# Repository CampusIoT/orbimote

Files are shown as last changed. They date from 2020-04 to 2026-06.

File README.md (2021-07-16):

# OrbiMote: open-sourced LoRaWAN high-altitude balloon (HAB) tracker

"urbi et orbi" : to the city and the world

The Orbimote is a LoRa/LoRaWAN endpoint
* for tracking sounding balloons
* and for implementing flying repeaters and flying field testers.

# HW & FW
* [Hardware](./hardware)
* [Firmware](./firmware)

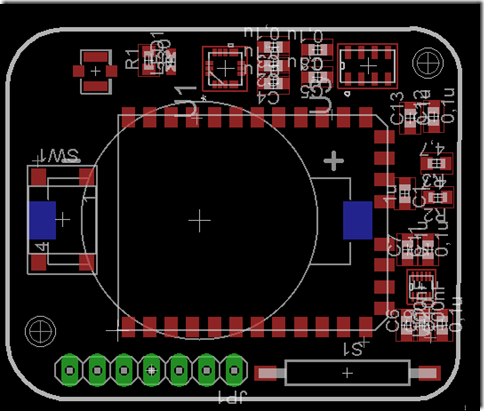
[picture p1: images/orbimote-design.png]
OrbiMote Schematic

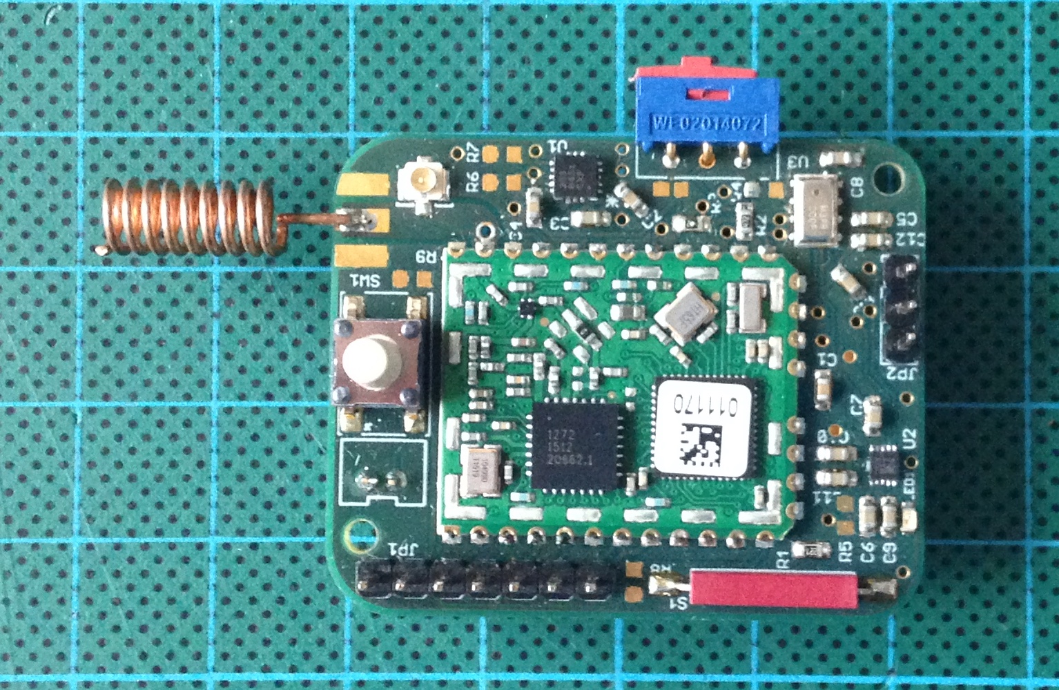
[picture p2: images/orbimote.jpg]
OrbiMote


## GNSS additional modules for near-space applications

According [CoCom](https://en.wikipedia.org/wiki/CoCom) regulations, most of commercial GPS modules stop at altitudes higher than 18000 meters and for speeds higher than 1000 knots (1852 km/h).

Here is a list of GPS modules : [gnss_modules.md](./gnss_modules.md)

## Barometers for near-space applications

Here is a list of barometer components and modules : [barometers.md](./barometers.md)

## Flights

[High-altitude flights](https://gricad-gitlab.univ-grenoble-alpes.fr/thingsat/public/-/blob/master/balloons)

### 2019
Valence, May 2019. [more](https://gricad-gitlab.univ-grenoble-alpes.fr/thingsat/public/-/blob/master/balloons/2019-05-09/README.md)
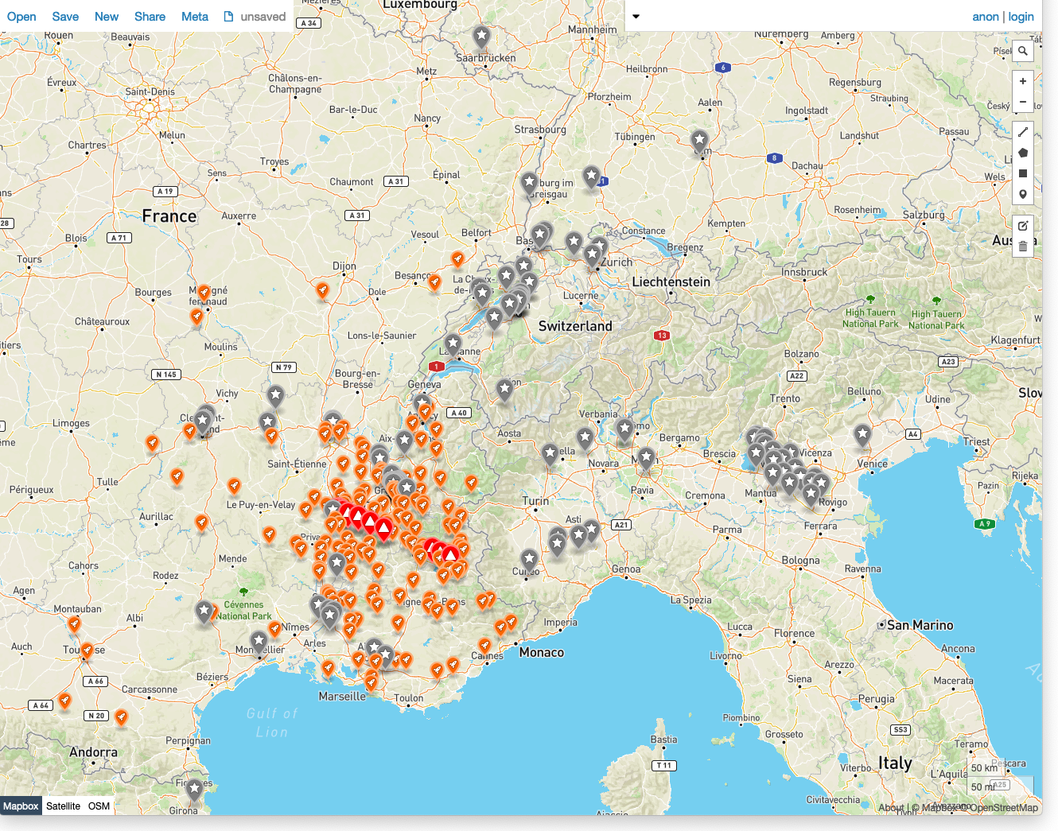
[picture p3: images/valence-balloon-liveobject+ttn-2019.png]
Valence

Legend: The balloon track (in red), Orange Liveobject stations (in orange), TTN stations (in grey)
### 2020
Aire-sur-l'Adour, September 2020. [more](https://gricad-gitlab.univ-grenoble-alpes.fr/thingsat/public/-/blob/master/balloons/2020-09-23/README.md)
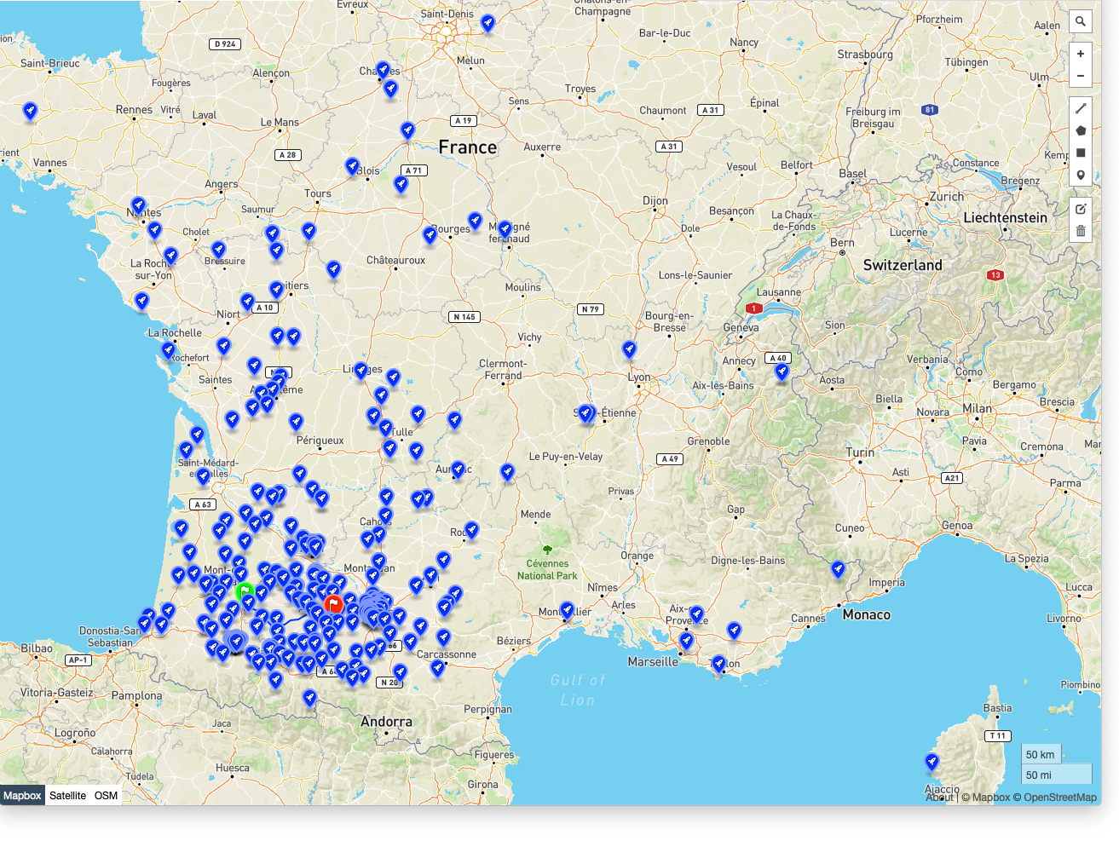
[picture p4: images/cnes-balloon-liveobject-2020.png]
Aire-sur-l'Adour

Legend: The balloon track (in green for departure, blue line and red for arrival), Orange Liveobject stations (in blue)

### 2021
Aire-sur-l'Adour, April 2021. [more](https://gricad-gitlab.univ-grenoble-alpes.fr/thingsat/public/-/blob/master/balloons/2021-04-15/README.md)
Aire-sur-l'Adour
Legend: The 3 balloons tracks (in green for departure, red for arrival), Orange Liveobject stations in orange, Requea stations in blue, Swisscom (thru Actility) in red.

## Altenatives
* [HAB2 High Altitude Balloon Tracker RFM9x](https://github.com/StuartsProjects/HAB2)

## Other usages
* Runners trackers
* Meshed-network of trail runners/trekers

## License
TBD

## Authors
* Didier DONSEZ
* Vivien QUEMA
* Gregory NOCERA

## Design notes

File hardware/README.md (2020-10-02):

# OrbiMote :: Hardware  

## Schematics   
* Done with [Eagle 7.7 Express](https://www.autodesk.com/products/eagle/free-download).

## Bill of material

* IMST iM880A
  * MCU: STM32L151CB - 128K FLASH, 10K RAM, Timers, SPI, I2C, USART, USB 2.0 full-speed device/host/OTG controller,DAC, ADC, DMA
  * RADIO: SX1272
* or [IMST iM880B-L](https://wireless-solutions.de/products/radiomodules/im880b-l.html)
* or [IMST iM881A-M](https://wireless-solutions.de/products/long-range-radio/im881a.html)
* MPL3115 : temperature, pressure
* MMA8451 : accelormeter
* MAG3110 : magnetometer
* reed switch
* button
* power switch
* SMA and UFL antenna connectors
* CR2032 battery holder
* plug for AA lithium battery
* pin header for JTAG/SWD
* pin header for RXTX

## Header for JTAG/SWD
Noted as JP1

    Pin 1 : GND
    Pin 2 : VCC
    Pin 3 : JTCK/SWCLK (pin 2 of the iM880a)
    Pin 4 : JTMS/SWDAT (pin 3 of the iM880a)
    Pin 5 : JTDO       (pin 4 of the iM880a)
    Pin 6 : JTDI       (pin 5 of the iM880a)
    Pin 7 : RESET      (pin 7 of the iM880a)

## Header for RXTX
Noted as JP2

    Pin 1 : GND
    Pin 2 : RX
    Pin 3 : TX

## GNSS additional modules for near-space applications

According [CoCom](https://en.wikipedia.org/wiki/CoCom) regulations, most of commercial GPS modules stop at altitudes higher than 18000 meters and for speeds higher than 1000 knots (1852 km/h).

Here is a list of GPS modules : [gnss_modules.md](../gnss_modules.md)

## Barometers for near-space applications

Here is a list of barometer components and modules : [barometers.md](../barometers.md)

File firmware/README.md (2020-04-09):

# OrbiMote :: Firmware

The OrbiMote firmware has been developed with [RIOTOS](https://github.com/RIOT-OS/RIOT) LoRaWAN stack and sensors drivers

## Board

### Module

* [boards/im880b](https://github.com/RIOT-OS/RIOT/tree/master/boards/im880b)

### Sensors

* [NXP MPL3115A2: 20 to 110 kPa, Absolute Digital Pressure Sensor](https://www.nxp.com/products/sensors/pressure-sensors/barometric-pressure-15-to-115-kpa/20-to-110-kpa-absolute-digital-pressure-sensor:MPL3115A2)
* [NXP MMA8451Q, 3-axis, 14-bit/8-bit digital accelerometer](https://www.nxp.com/docs/en/data-sheet/MMA8451Q.pdf)
* [NXP Xtrinsic MAG3110 Three-Axis, Digital Magnetometer](https://www.nxp.com/docs/en/data-sheet/MAG3110.pdf)
* Push button
* Reed switch
* [GNSS module on UART](../gnss_modules.md) (instead of console)

## Build and flash 

By default, the DevEUI, the AppEUI and the AppKey are forged using the CPU ID of the MCU. However, you can set the DevEUI, the AppEUI and the AppKey of the LoRaWAN endpoint into the `main.c`.

Optional : Configure the following parameters into the program file `main.c` : `FIRST_TX_PERIOD`, `TX_PERIOD`, `DR_INIT`, `ADR_ON`, `DEBUG_ON` and `SECRET`.

Register the endpoint into a LoRaWAN network (public or private) using the DevEUI, the AppEUI and the AppKey

Build the firmware
```bash
export RIOT_BASE=~/github/RIOT-OS/RIOT
make binfile
```
Connect the JP1 board pins to the STLink according the [JTAG-SWD wiring](hardware/README.md#header-for-jtagswd) and then flash the firmware
```bash
export RIOT_BASE=~/github/RIOT-OS/RIOT
make flash
```
## Console
Connect the JP2 TX pin to USBSerial port and then configure and start `minicom`.

```bash
ll /dev/tty.*
minicom -s
```

## AppKey

The AppKey can be recovered from the DevEUI (displayed at startup) and the SECRET (flashed into the firmware) with the command lines below:

```bash
SECRET=cafebabe02000001cafebabe02ffffff                                         
DevEUI=33323431007f1234                                                         
AppEUI=33323431ffffffff                                                        
SHA=$(echo -n $DevEUI$AppEUI$SECRET | xxd -r -p | shasum -b | awk '{print $1}')
AppKey="${SHA:0:32}"
echo $AppKey
```

## Downlink

You can send a downlink message to the endpoint throught your network server.

Downlink payload can be used for
* sending an ASCII message (port = 1)
* setting the realtime clock of the endpoint (port = 2)
* setting the tx period of the data (port = 3)

### Setup
For CampusIoT:
```bash
ORGID=<YOUR_ORG_ID>
BROKER=lora.campusiot.imag.fr
MQTTUSER=org-$ORGID
MQTTPASSWORD=<YOUR_ORG_TOKEN>
applicationID=1
devEUI=1234567890abcdef
```

### sending an ASCII message
```bash
PORT=1
mosquitto_pub -h $BROKER -u $MQTTUSER -P $MQTTPASSWORD -t "application/$applicationID/device/$devEUI/tx" -m '{"reference": "abcd1234","confirmed": true, "fPort": '$PORT',"data":"SGVsbG8gQ2FtcHVzSW9UICE="}'
```

The output on the console is:
```bash
main(): This is RIOT! (Version: 2020.04-devel-1660-gb535c)
Secret:cafebabe02000001cafebabe02ffffff                                         
DevEUI:33323431007f1234                                                         
AppEUI:33323431ffffffff                                                         
AppKey:f482a62f0f1234ac960882a2e25f971b                                         
Starting join procedure: dr=5                                                   
Join procedure succeeded                                                        
Sending LPP payload with : T: 22.75                                             
Received ACK from network                                                       
Sending LPP payload with : T: 22.75                                             
Data received: Hello CampusIoT !, port: 1                                      
Received ACK from network                                                       
```

### Setting the realtime clock of the endpoint
```bash
PORT=2
mosquitto_pub -h $BROKER -u $MQTTUSER -P $MQTTPASSWORD -t "application/$applicationID/device/$devEUI/tx" -m '{"reference": "abcd1234","confirmed": true, "fPort": '$PORT',"data":"5UKHXg=="}'
```

> The epoch is a unsigned 32 bit-long integer (big endian)

The output on the console is:
```bash
...
Received ACK from network                                                       
Clock value is now   2000-01-01 00:00:36
Sending LPP payload with : T: 22.50                                             
Data received: epoch=1585922789, port: 2                                        
Clock value is set to   2020-04-03 14:06:29                                     
Clock value is now   2020-04-03 14:06:29                                        
Received ACK from network                                                       
```

### setting the tx period of the data

```bash
PORT=3
mosquitto_pub -h $BROKER -u $MQTTUSER -P $MQTTPASSWORD -t "application/$applicationID/device/$devEUI/tx" -m '{"reference": "abcd1234","confirmed": true, "fPort": '$PORT',"data":"PAA="}'
```
> The new tx period is 60 seconds (3C00)
> The epoch is a unsigned 16 bit-long integer (big endian)

The output on the console is:
```bash
...
Sending LPP payload with : T: 22.75                                
Data received: tx_period=60, port: 3                                            
Received ACK from network                                                       
```

## References
* https://github.com/CampusIoT/tutorial/tree/master/riotos
* https://github.com/CampusIoT/tutorial/tree/master/im880a

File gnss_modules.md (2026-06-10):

# GNSS modules for balloon tracking

According [CoCom](https://en.wikipedia.org/wiki/CoCom) regulations, most of commercial GPS modules stop at altitudes higher than 18000 meters and for speeds higher than 1000 knots (1852 km/h).

## Quectel

[Balloon mode modules](https://www.quectel.com/gnss-iot-modules): L70-R, L70-RL, L76, L96
### Quectel L80 GPS Module
* https://www.quectel.com/product/l80.htm
* https://www.gotronic.fr/art-shield-lora-et-gps-113990254-27806.htm#complte_desc
* 14 euros chez RS https://fr.rs-online.com/web/p/puces-gps-et-modules-gps/9084085/
* 7 USD chez Avnet https://www.avnet.com/shop/us/products/quectel-wireless-solutions/l80-m39-3074457345626708837/
* 49 euros chez [MIKROE-1714](https://fr.farnell.com/mikroelektronika/mikroe-1714/carte-add-on-gps3-click/dp/2521701)

### Quectel L76-L GPS Module

* Balloon mode, for high altitude up to 80km
* Module on [Pycom PyTrack](https://github.com/pycom/pycom-libraries/tree/master/shields) and [Dragino LGT92](https://www.dragino.com/products/lora-lorawan-end-node/item/142-lgt-92.html)

* [Documents](https://www.quectel.com/product/gnss-l76/)

### Quectel L96-L GPS Module
* Balloon mode, for high altitude up to 80km
* embedded Mediatek MT3333 GNSS chip

* [L96EVB-KIT eval board](https://www.digikey.fr/fr/products/detail/quectel/L96EVB-KIT)
  
## U-Blox

### U-Blox NEO-M6 series

* [TTGO T-BEAM Tracker LoRa GPS tracker]()

#### U-Blox NEO-6M-0-001

> Warming: [some module labeled NEO-6M-0-001 bought at Aliexpress are fake](https://portal.u-blox.com/s/question/0D52p00008eQuqZCAS/neo6m-spi-problem-solved) :

```
$GPTXT,01,0?$GPTXT,01,01,02,u-blox ag - www.u-blox.com*50
$GPTXT,01,01,02,HW  UBX-G5xxx  00040005 FF59FFFFp*67
$GPTXT,01,01,02,ROM CORE 5.00 (28483) Jun  6 2008 14:45:11*40
$GPTXT,01,01,02,ANTSUPERV=AC SD PDoS SR*20
```

#### GY-NEO6MV2

> Note: The GY-NEO6MV2 modules available on Aliexpress require a 5V VCC and baudrate is 9600. 

### MAX-7

[RAK1910 : GNSS GPS Location Module u-Blox MAX-7Q](https://store.rakwireless.com/products/rak1910-max-7q-gnss-location-sensor) Altitude max : 50,000 m

### M8

### U-Blox NEO-M8 series

* https://www.u-blox.com/en/product/neo-m8-series¨
* https://www.u-blox.com/en/positioning-chips-and-modules#tab-standard-precision-gnss

#### U-Blox SAM-M8Q
    up to 50000 m
    
* https://www.sparkfun.com/products/15210
* https://cdn.sparkfun.com/assets/4/e/b/9/f/SAM-M8Q_DataSheet__UBX-16012619_.pdf
* https://cdn.sparkfun.com/assets/5/d/d/2/3/SAM-M8Q_HardwareIntegrationManual__UBX-16018358_.pdf
* [RAK5146 LoRa Gateway](https://store.rakwireless.com/products/wislink-concentrator-module-sx1303-rak5146-lorawan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) : Built-in ZOE-M8Q GPS module

### ZED-F9 (RTK)

#### ZED-F9P

* up to 80000 m

* https://www.u-blox.com/en/product/zed-f9p-module
* [GPS RTK (Real Time Kinematics)@Sparkfun](https://learn.sparkfun.com/tutorials/what-is-gps-rtk/all)

## ADH

* http://www.adh-tech.com.tw

### ADH GP-635T

* up to 50000 m

* Sparkfun GP-735 https://www.sparkfun.com/products/13670 https://cdn.sparkfun.com/datasheets/GPS/GP-735T-150203.pdf
* https://www.generationrobots.com/media/GP-635T-121130-datasheet.pdf

## Sierra Wireless

### AirPrime XA1110

80,000m maximum (Balloon mode)

[SparkFun GPS Breakout - XA1110 (Qwiic)](https://learn.sparkfun.com/tutorials/sparkfun-gps-breakout---xa1110-qwiic-hookup-guide/hardware-overview)

https://cdn.sparkfun.com/assets/parts/1/2/2/8/0/GlobalTop_Titan_X1_Datasheet.pdf

Interface : UART (9600, 115200), I2C

LOCUS : internal 2 days log

## MediaTek

### MediaTek X1110

    80,000m maximum (Balloon mode)
    AT Command to Enter balloon mode : $PMTK886,3*2B<CR><LF>

* https://cdn.sparkfun.com/assets/parts/1/2/2/8/0/GlobalTop_Titan_X1_Datasheet.pdf
* https://cdn.sparkfun.com/assets/parts/1/2/2/8/0/PMTK_Packet_User_Manual.pdf
* https://www.sparkfun.com/products/14414
* https://learn.sparkfun.com/tutorials/sparkfun-gps-breakout---xa1110-qwiic-hookup-guide

## Stoton

### Stoton GN-801

    u-blox 8 UBX-M8030-KT chipset
    3.3V and 5V
    baudrate 9600
    The color of the wires are wrong (red and black) !!!!!

* http://www.stotoncn.com/gnssmodule/showproduct.php?lang=en&id=42
* http://www.stotoncn.com/upload/file/201801/1516180733487356.pdf

### Stoton GG-1802
    
    UBX-8030-KT chipset

* http://www.stotoncn.com/gnssmodule/showproduct.php?lang=en&id=63

## MTK3339 chipset

Default baudrate :  9600 bps

https://cdn.sparkfun.com/assets/parts/1/2/2/8/0/PMTK_Packet_User_Manual.pdf

‘3’: Balloon mode: For high-altitude balloon purpose that the vertical movement will have more effect
on the position calculation.
```
$PMTK886,3*2B<CR><LF> :Enter balloon mode.
Return: $PMTK001,886,3*36<CR><LF>
```
* [Adafruit Ultimate GPS v3](https://www.adafruit.com/product/746) [manual](https://cdn-learn.adafruit.com/downloads/pdf/adafruit-ultimate-gps.pdf)

## Globalsat

### Globalsat ET-662

    up to 18000m
    
* https://www.avrfreaks.net/sites/default/files/ET-662%20user%20manual%20V2.2.pdf

## Simcom

### Simcom SIM28

    Alimentation en 5V DC sur le platine [Grove GPS](http://wiki.seeedstudio.com/Grove-GPS/)
    Baudrate 9600 (et non 4800 par défaut)
    Altitude max 11000 m lors du vol depuis Valence

* https://www.tme.eu/Document/f3c28c977bbaeda48f88a1b8bb1a2a89/SIMCom%20Module%20%20EVB%20Kit.pdf
* https://www.tme.eu/Document/a5741a672d9b6a08eb0788fdbd1537f4/SIM28.pdf
* https://simcom.ee/documents/SIM28ML/SIM28ML_Hardware%20Design_V1.01.pdf
* http://www.vis-plus.ee/pdf/SIMCOM_SIM5350_ATC_EN_V1.02.pdf

## ST Microelectronics

### ST Teseo-LIV3F

    multiple constellations (GPS/Galileo/Glonass/BeiDou/QZSS).
    I2C, UART
    NMEA protocol
    mode ballon ?

* [Teseo-LIV3F Tiny GNSS module ](https://www.st.com/content/st_com/en/products/positioning/gnss-modules/teseo-liv3f.html)
* [X-NUCLEO-GNSS1A1 GNSS expansion board based on Teseo-LIV3F module for STM32 Nucleo](https://www.st.com/en/ecosystems/x-nucleo-gnss1a1.html)
* STEVAL-STRKT01 https://www.st.com/content/st_com/en/products/evaluation-tools/solution-evaluation-tools/communication-and-connectivity-solution-eval-boards/steval-strkt01.html
* https://stm32python.gitlab.io/fr/docs/Stm32duino/exercices/x-nucleo-gnss1a1

## Air530
* [Grove - GPS (Air530)](https://wiki.seeedstudio.com/Grove-GPS-Air530/) ([wiki](https://wiki.openluat.com/))

## AT6558R
[doc](https://www.icofchina.com/d/file/xiazai/2016-12-05/b1be6f481cdf9d773b963ab30a2d11d8.pdf)

in Dragino LGT92

```
$GPTXT,01,01,02,MA=CASIC*27
$GPTXT,01,01,02,IC=AT6558R-5N-52-1C580901*15
$GPTXT,01,01,02,SW=URANUS5,V5.3.0.0*1D
$GPTXT,01,01,02,TB=2020-03-26,13:25:12*4B
$GPTXT,01,01,02,MO=GR*67
```

## GNSS evaluation software for Windows
* https://www.u-blox.com/en/product/u-center

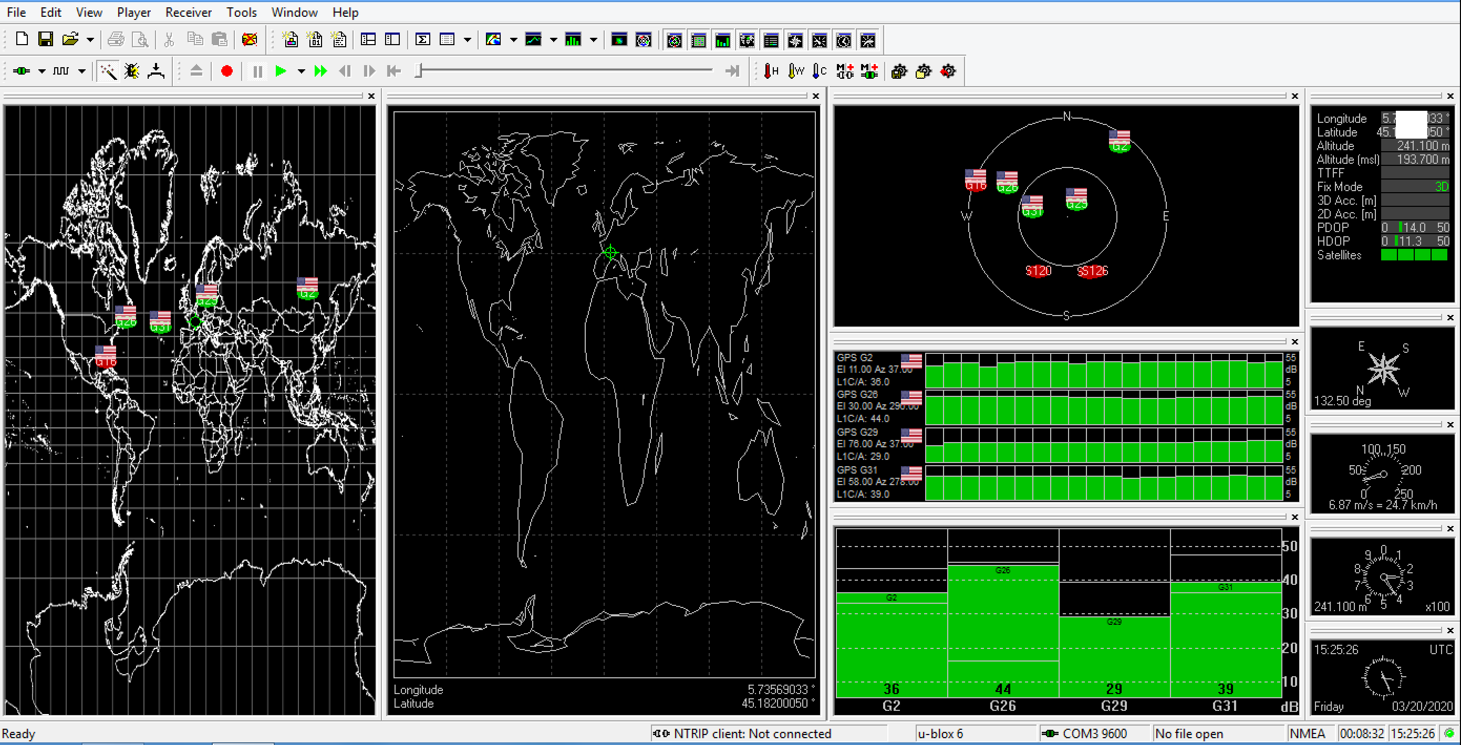
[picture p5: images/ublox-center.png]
u-center

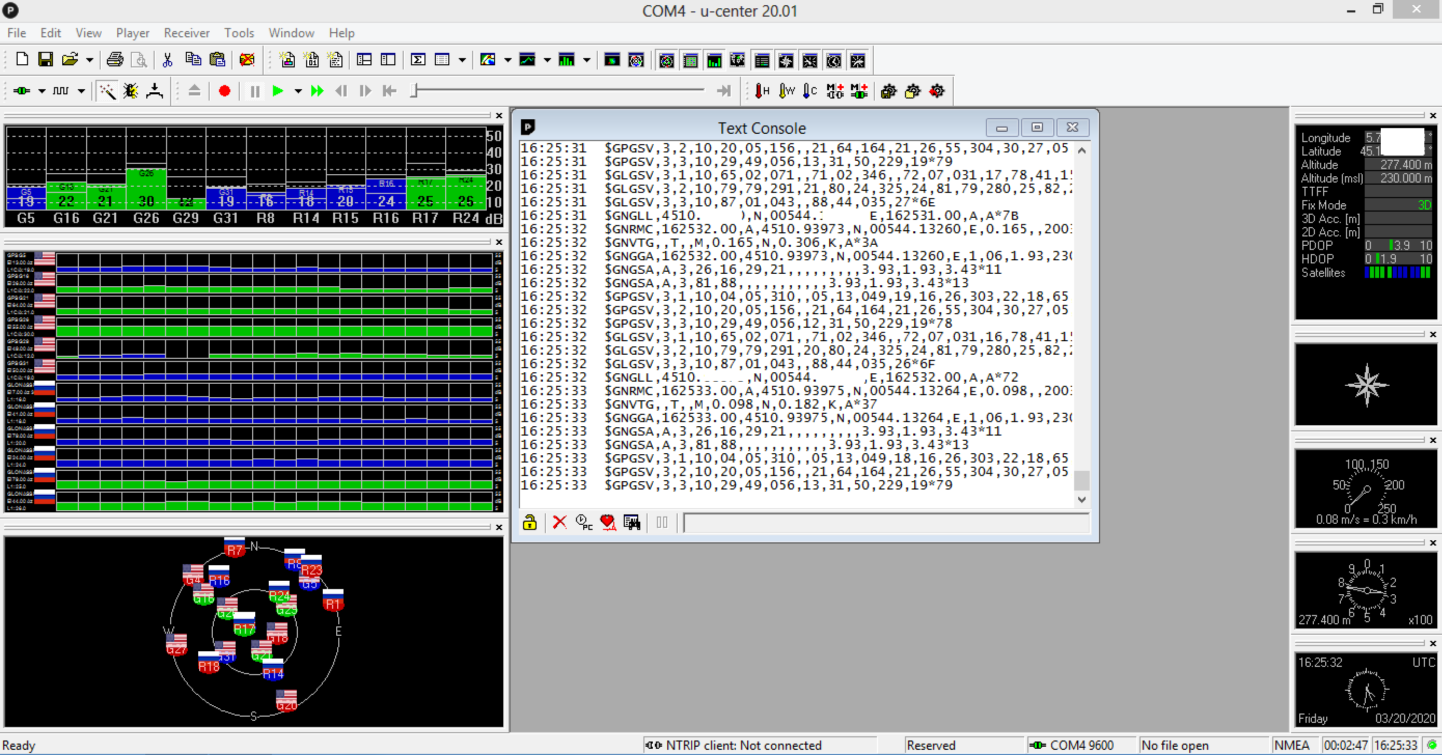
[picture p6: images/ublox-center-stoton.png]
u-center Stoton


## See also
* [Stuart Robinson, Comparison of High Altitude Balloon GPSs](https://github.com/StuartsProjects/GPSTutorial/tree/master/GPS%20performance%20comparisons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)

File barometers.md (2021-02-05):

# Barometers for near-space applications

Barometers enable to compute the altitude from temperature and atmospheric pressure ([cf formulea](https://en.wikipedia.org/wiki/Pressure_altitude)).

Typical values ([From](https://www.engineeringtoolbox.com/air-altitude-pressure-d_462.html)):
| Altitude (m) | Temperature (°C) | Pressure (hPa) |
| ---:| ---:| ---:|
| 0 |  15 | 1010 |
| 1000  |  ?? | 890  |
| 2000  |  ?? | 790  |
| 4000  |  ?? | 600 |
| 8000  |  ?? | 360 |
| 10000 |  ?? | 240 |
| 15000 |  ?? | 110 |
| 20000 |  ?? | TBC |
| 25000 |  ?? | TBC |
| 30000 |  ?? | TBC |
| 35000 |  ?? | TBC |

## Components
| Component | Sensors | Range (Resolution) | Breakouts, Boards | OS support | Status  |
| --- | --- | --- | --- | --- | ----- |
| [Bosch BMP280](https://www.bosch-sensortec.com/products/environmental-sensors/pressure-sensors/pressure-sensors-bmp280-1.html) | Temperature, Pressure| 300 to 1100 hPa (0.01 hPa), -40-85°C (0.01° C)| TBC | RIOT | Active |
| [Bosch BME680](https://cdn.sparkfun.com/assets/8/a/1/c/f/BME680-Datasheet.pdf) | Humidity, Barometric pressure, Temperature and Indoor Air Quality| 300 to 1100 hPa (0.01 hPa)| TBC | RIOT | Active |
| [STM LPS27HHW](https://www.st.com/en/mems-and-sensors/lps27hhw.html) | Pressure | 260 to 1260 hPa (0.5 hPa RMS) | TBC | TBC | Active |
| [STM LPS25HB](https://www.st.com/en/mems-and-sensors/lps25hb.html) | Pressure | 260 to 1260 hPa (0.01 hPa RMS) | TBC | TBC | Active |
| [STM LPS22HB](https://www.st.com/en/mems-and-sensors/lps22hb.html) | Pressure | 260 to 1260 hPa (0.01 hPa RMS) | TBC | TBC | Active |
| [Murata SCP1000-D01](https://www.sparkfun.com/products/retired/8161) | Pressure | 300 hPa to 1200 hPa, -20C to 70C | TBC | TBC | Obsolete |
| [Murata ZPA2326-0311A-R](https://www.murata.com/en-eu/products/productdetail?partno=ZPA2326-0311A-R) | Pressure | 800 to 1100hPa (0.01 hPa) | TBC | TBC | Active |
| [Amphenol Pressure Sensors](https://www.amphenol-sensors.com/en/mems-pressure-sensors) | Pressure | TBC| TBC | TBC | Active |
| [NXP MPL115A](https://www.nxp.com/products/sensors/pressure-sensors/barometric-pressure-15-to-115-kpa/50-to-115kpa-absolute-digital-pressure-sensor:MPL115A) | Pressure | 500 hPa to 1150 hPa| TBC | TBC | Active |
| [NXP MPL3115A2](https://www.nxp.com/products/sensors/pressure-sensors/barometric-pressure-15-to-115-kpa/20-to-110-kpa-absolute-digital-pressure-sensor:MPL3115A2) | Pressure | 200 hPa to 1100 hPa| TBC | RIOT | Active |
| [TE MS5637-02BA03](https://cdn.sparkfun.com/assets/1/1/d/b/e/MS5637_Datasheet.pdf) | Pressure | 300 hPa to 1200 hPa| TBC | TBC | Active |

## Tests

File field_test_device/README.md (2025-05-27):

# Field Test Device

## Field Test Device

The program sends periodically LoRaWAN frames at various datarate and tx power.

If a NMEA0183 GNSS module is plugged onto the board, the postion is sent into each LoRaWAN frames. See the list of [NMEA0183 GNSS module](../gnss_modules.md).

Uplink frames can be confirmed or unconfirmed by the network server.

The RTC of the board can be synchronized according to the [App Clock Sync Specification](https://lora-alliance.org/resource-hub/lorawanr-application-layer-clock-synchronization-specification-v100).

## Payload format

	fPort : 2 to 170
	
	uint8 : txpower idx (1 .. 7) related to the Txpower table into the Regional Parameters spec
	uint8 : datarate (0,1,2,3,4,5)
	int16 : temperature in 0.01 °C
	int24 : latitude
	int24 : longitude
	int16 : altitude

> The paylaod will include in a future version the following fields : downlink message counter (uint16_t), last downlink fCnt (uint16_t), last downlink RSSI (uint8_t), last downlink LSNR (int8_t) and GPIO_IN bitfield (uint8_t)

## Boards

Board:
* [x] [boards/im880b](https://github.com/RIOT-OS/RIOT/tree/master/boards/im880b)
* [x] [OrbiMote (im880a)](https://github.com/CampusIoT/orbimote)
* [x] [nucleo-f446re](https://github.com/RIOT-OS/RIOT/tree/master/boards/nucleo-f446re) + [P-NUCLEO-LRWAN1](https://www.st.com/en/evaluation-tools/p-nucleo-lrwan1.html)
* [x] [nucleo-f446re](https://github.com/RIOT-OS/RIOT/tree/master/boards/nucleo-f446re) + [SX1276MB1xAS](https://os.mbed.com/components/SX1276MB1xAS/) for eu433 and eu868
* [ ] [nucleo-f446re](https://github.com/RIOT-OS/RIOT/tree/master/boards/nucleo-f446re) + [Semtech LLCC68 MBed shield](https://github.com/RIOT-OS/RIOT/tree/master/drivers/sx126x)
* [x] [boards/b-l072z-lrwan1](https://github.com/RIOT-OS/RIOT/tree/master/boards/b-l072z-lrwan1)
* [x] [Nucleo WL55JC EU868](https://github.com/RIOT-OS/RIOT/tree/master/boards/nucleo-wl55jc)
* [x] [Nucleo WL55JC2 EU433](https://github.com/RIOT-OS/RIOT/tree/master/boards/nucleo-wl55jc)
* [ ] [Seeedstudio LoRa E5 Dev](https://github.com/RIOT-OS/RIOT/tree/master/boards/lora-e5-dev)
* [ ] [Seeedstudio LoRa E5 Mini](https://github.com/RIOT-OS/RIOT/tree/master/boards/lora-e5-mini)
* [ ] [ESP32 Heltec LoRa](https://github.com/RIOT-OS/RIOT/tree/master/boards/esp32-heltec-lora32-v2)
* [ ] [ESP32 TTGO Beam](https://github.com/RIOT-OS/RIOT/blob/master/boards/esp32-ttgo-t-beam)
* [ ] [Bluepill](https://github.com/RIOT-OS/RIOT/tree/master/boards/bluepill-stm32f030c8) + [RFM9x](https://learn.adafruit.com/adafruit-rfm69hcw-and-rfm96-rfm95-rfm98-lora-packet-padio-breakouts/arduino-wiring)
* [ ] [Generic Node](https://www.genericnode.com/)
* [ ] [Dragino LGT92 GPS Tracker](https://www.dragino.com/products/lora-lorawan-end-node/item/142-lgt-92.html) : STM32L072, [Quectel GNSS L76-L](https://www.quectel.com/product/gnss-l76-l/) + [TDK MPU 9250](https://invensense.tdk.com/products/motion-tracking/9-axis/mpu-9250/)
* [ ] LilyGo (SX1262)
* [ ] all boards with [Microchip RN2483 module](https://github.com/RIOT-OS/RIOT/tree/master/drivers/rn2xx3)
* [x] Idosens Sensor (SX1276)
* [x] Idosens Remote (SX1276)
* [x] Idosens Base (SX1276) add ePaper Display Driver

### Default board

The IMST iM880a board is a simple prototyping board with an IMST IMST iM880a LoRa module 
a DS75LX temperature sensor. The TX pin of a [NMEA0183 GNSS module](../gnss_modules.md) can be plugged on the pin 10 (Rx) of connector X2 (with 3V3 on pin 11 and GND on pin 12).

<p align="center">
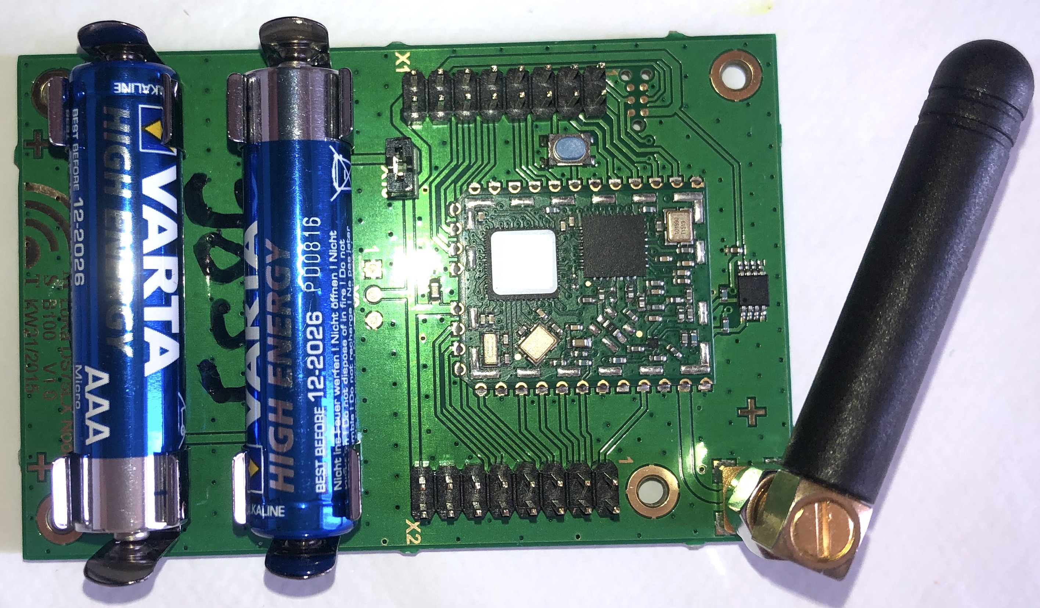
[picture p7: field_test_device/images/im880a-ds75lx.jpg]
iM880a-DS75LX

</p>

## Libraries

Packages & Drivers:
* [semtech-loramac](https://github.com/RIOT-OS/RIOT/tree/master/pkg/semtech-loramac)
* [cayenne-lpp](https://github.com/RIOT-OS/RIOT/tree/master/pkg/cayenne-lpp)
* [ds75lx](https://github.com/RIOT-OS/RIOT/tree/master/drivers/ds75lx)

GPS modules:
* [See notes](../gnss_modules.md)

## Build and flash

### Build and flash for Nucleo WL55JC (`BOARD=nucleo-wl55jc`)

Build and flash the firmware
```bash
export RIOTBASE=~/github/RIOT-OS/RIOT
make BOARD=nucleo-wl55jc flash
```

> Remark: The version of `openocd` should be `0.11.0+`

### Build and flash for Nucleo WL55JC2 ISM 433 MHz  (`BOARD=nucleo-wl55jc REGION=EU433`)

Build and flash the firmware
```bash
export RIOTBASE=~/github/RIOT-OS/RIOT
make BOARD=nucleo-wl55jc REGION=EU433 flash
```

> Remark: The version of `openocd` should be `0.11.0+`

### Build and flash for IMST iM880 a and b (`BOARD=im880b`)

Connect the X1 and X2 connectors according to the wiring despicted in the annexes.

Register the endpoint into a LoRaWAN network (public or private) using the DevEUI, the AppEUI and the AppKey (displayed into the console).

Build the firmware
```bash
export RIOTBASE=~/github/RIOT-OS/RIOT
make binfile
```

Connect the board to the STLink according this [tutorial](https://github.com/CampusIoT/tutorial/tree/master/im880a) and then flash the firmware
```bash
export RIOTBASE=~/github/RIOT-OS/RIOT
make flash-only
```

### Build and flash for Seeedstudio LoRa E5 Dev and Mini (`BOARD=lora-e5-dev`)

Build the firmware
```bash
export RIOTBASE=~/github/RIOT-OS/RIOT
make BOARD=lora-e5-dev
```

Connect the board to the SWD connector of the programmer.

Flash : [STM32CubeProgrammer](https://www.st.com/en/development-tools/stm32cubeprog.html) + STLink v2

> NB: The [`seed_lora-e5-mini`](https://gricad-gitlab.univ-grenoble-alpes.fr/thingsat/seed/-/blob/main/seed_lora-e5-mini/README.md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) board includes 1x [BME680](https://www.bosch-sensortec.com/products/environmental-sensors/gas-sensors/bme680/) and 2x [ADS1115](https://www.ti.com/product/ADS1115)

### Build and flash for Nucleo WL55JC (`BOARD=nucleo-wl55jc`)

TODO

Two boards : Nucleo WL55JC1 (eu868) and Nucleo WL55JC2 (eu433)

### Build and flash for Discovery B-L072Z-LRWAN1 (`BOARD=b-l072z-lrwan1`)

Build and flash the firmware
```bash
export RIOTBASE=~/github/RIOT-OS/RIOT
make BOARD=b-l072z-lrwan1 LORA_DRIVER=sx1276 flash
```

## Setting DEVEUI APPEUI APPKEY

By default, the DevEUI, the AppEUI and the AppKey are forged using the CPU ID of the MCU. However, you can set the DevEUI, the AppEUI and the AppKey of the LoRaWAN endpoint into the `main.c`.

Optional : Configure the following parameters into the program file `main.c` : `FIRST_TX_PERIOD`, `TX_PERIOD`, `DR_INIT`, `ADR_ON`, `DEBUG_ON` and `SECRET`.
```bash
make SECRET=cafebabe02ffffffcafebabe02000001 binfile
```

The AppKey can be recovered from the DevEUI (displayed at startup) and the SECRET (flashed into the firmware) with the command lines below:
```bash
SECRET=cafebabe02000001cafebabe02ffffff                                         
DevEUI=33323431007f1234                                                         
AppEUI=33323431ffffffff                                                        
SHA=$(echo -n $DevEUI$AppEUI$SECRET | xxd -r -p | shasum -b | awk '{print $1}')
AppKey="${SHA:0:32}"
echo $AppKey
```

The DevEUI, the AppEUI and the AppKey can be set by fixing DEVEUI APPEUI APPKEY into the `make` command
```bash
DevEUI=33323431007f1234
AppEUI=33323431ffffffff
AppKey=f482a62f0f1234ac960882a2e25f971b
make DEVEUI=$DevEUI APPEUI=$AppEUI APPKEY=$AppKey binfile
```

## Enable/Disable the GNSS module

Edit Makefile or overload GPS and STD_BAUDRATE default values 
```bash
GPS=0 make
GPS=1 STD_BAUDRATE=9600 make
GPS=1 STD_BAUDRATE=56700 make
```

> if GPS is enabled, the console baudrate is 9600 b/s and not by default 115200 b/s.

## Enable/Disable the region duty cycle

The region duty cycle can be enabled or disabled in the region file in `bin/pkg/im880b/semtech-loramac/src/mac/region`.

For instance, `~/github/RIOT-OS/RIOT/build/pkg/semtech-loramac/src/mac/region/RegionEU868.h` for region `EU868`

Enable region duty cycle
```c
#define EU868_DUTY_CYCLE_ENABLED                    1
```

Disable region duty cycle
```c
#define EU868_DUTY_CAAYCLE_ENABLED                    0
```

## Console
Connect the board TX pin to USBSerial port and then configure and start `minicom` or `Pyterm` or `tio`.

> if GPS is enabled, the baudrate is 9600 b/s. Else the baudrate is 115200 b/s.

```bash
ll /dev/tty.*
make term
```

or

```bash
ll /dev/tty.*
minicom -s
```

or
```bash
brew install tio
tio -L
tio -b 115200 -m INLCRNL /dev/tty.usbserial-142xxx
```

## Downlink

The application can send a downlink message to the endpoint throught your network server.

Downlink payload can be used for
* sending an ASCII message (port = 1)
* setting the realtime clock of the endpoint (port = 2)
* setting the tx period of the data (port = 3)

### Setup
For CampusIoT:
```bash
ORGID=<YOUR_ORG_ID>
BROKER=lns.campusiot.imag.fr
MQTTUSER=org-$ORGID
MQTTPASSWORD=<YOUR_ORG_TOKEN>
applicationID=1
devEUI=33323431007f1234
```

### sending an ASCII message
```bash
PORT=1
mosquitto_pub -h $BROKER -u $MQTTUSER -P $MQTTPASSWORD -t "application/$applicationID/device/$devEUI/tx" -m '{"reference": "abcd1234","confirmed": true, "fPort": '$PORT',"data":"SGVsbG8gQ2FtcHVzSW9UICE="}'
```

The output on the console is:
```bash
main(): This is RIOT! (Version: 2020.04-devel-1660-gb535c)
Secret:cafebabe02000001cafebabe02ffffff                                         
DevEUI:33323431007f1234                                                         
AppEUI:33323431ffffffff                                                         
AppKey:f482a62f0f1234ac960882a2e25f971b                                         
Starting join procedure: dr=5                                                   
Join procedure succeeded                                                        
Sending LPP payload with : T: 22.75                                             
Received ACK from network                                                       
Sending LPP payload with : T: 22.75                                             
Data received: Hello CampusIoT !, port: 1                                      
Received ACK from network                                                       
```

### setting the tx period of the data

```bash
PORT=3
mosquitto_pub -h $BROKER -u $MQTTUSER -P $MQTTPASSWORD -t "application/$applicationID/device/$devEUI/tx" -m '{"reference": "abcd1234","confirmed": true, "fPort": '$PORT',"data":"PAA="}'
```
> The new tx period is 60 seconds (3C00)
> The epoch is a unsigned 16 bit-long integer (big endian)

The output on the console is:
```bash
...
Sending LPP payload with : T: 22.75                                
Data received: tx_period=60, port: 3                                            
Received ACK from network                                                       
```

### Setting the realtime clock of the endpoint
```bash
PORT=202
PAYLOAD=FE0BF6FB4B
mosquitto_pub -h $BROKER -u $MQTTUSER -P $MQTTPASSWORD -t "application/$applicationID/device/$devEUI/tx" -m '{"reference": "abcd1234","confirmed": true, "fPort": '$PORT',"data":"/gv2+0s="}'
```

> The time is the number of seconds since 06/01/1980 (GPS start time). It is unsigned 32 bit-long integer (big endian) LSBF 

The output on the console is:
```bash
...
Received ACK from network                                                                                 
Current RTC time :   2020-05-24 15:03:09                                                                  
Last correction  :   2020-05-24 15:00:49                                                                  
Read temperature= 25.00                                                                                   
app_clock_process_downlink                                                                                
X_APP_CLOCK_CID_AppTimeSetReq                                                                             
Current time    :   2020-05-24 15:03:44                                                                   
RTC time fixed  :   2020-05-24 16:08:43                                                                   
sent_buffer:                                                                                              
```

> Remark: Chirpstack implements the [App Clock Sync Specification](https://lora-alliance.org/resource-hub/lorawanr-application-layer-clock-synchronization-specification-v100). The synchronization is done at the LNS level.

### Rebooting on downlink

The application can send a reboot downlink message to the endpoint throught your network server.

* Send a downlink message on port 64 reboots the board immedialy
* Send a downlink message on port 65 reboots the board after 1 minute
* Send a downlink message on port 66 reboots the board after 1 hour

## Annexes

## TODO
* [ ] Add a downlink message counter (uint16_t), the last downlink fCnt (uint16_t), last downlink RSSI (uint8_t), last downlink LSNR (int8_t) and GPIO_IN bitfield (uint8_t)  into the uplink payload
* [x] Downlink for configuring TxPeriod
* [ ] Downlink for reading GPIO_IN
* [ ] Downlink for setting GPIO_OUT (set or clear) for actuator control
* [ ] Downlink for configuring the DRPWSZ_SEQUENCE
* [ ] Downlink for configuring Confirmation
* [ ] Downlink for rejoining (see Certification Test)
* [ ] Downlink for setting ADR (see Certification Test)
* [ ] Class C endpoint -> `semtech_loramac_set_class(&loramac, LORAMAC_CLASS_C);
* [ ] Class B endpoint -> `semtech_loramac_set_class(&loramac, LORAMAC_CLASS_B);`
* [ ] Multiple ABP endpoints with DEVADDRS define
* [x] Reboot downlink message.
* [ ] Send a confirmed uplink message for confirming the reboot
 
## Base64 utils
Encode base64
```bash
echo 'Hello CampusIoT' | base64
echo '414243442045464748' | xxd -r -p | base64
```

Decode base64
```bash
echo SGVsbG8gQ2FtcHVzSW9UCg== | base64 -d
echo QUJDRCBFRkdI | base64 -d
```

### IMST iM880a DS75LX Connectors

<p align="center">
iM880a-DS75LX
</p>

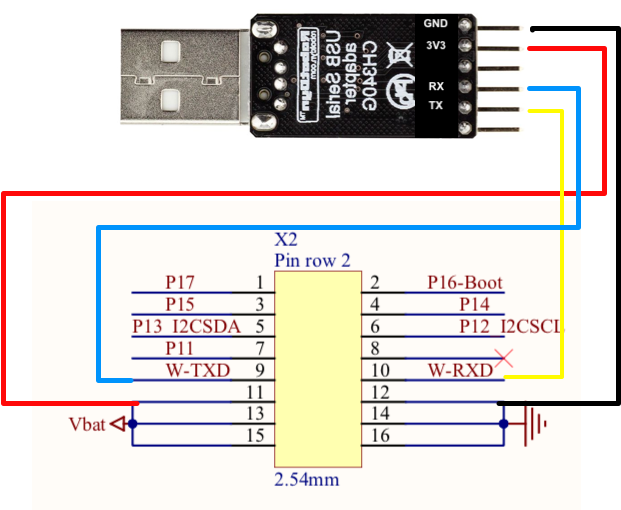
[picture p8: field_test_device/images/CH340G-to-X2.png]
Connector X1


Connector X1

Connector X2

Connector X2

> Note: if you do not have an ST-Link v2 flasher, you can use the ST-Link part of a Nucleo board and connect the first 5 pins of the [CN4 SWD connector](https://www.st.com/content/ccc/resource/technical/document/user_manual/98/2e/fa/4b/e0/82/43/b7/DM00105823.pdf/files/DM00105823.pdf/jcr:content/translations/en.DM0010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) to the X1 connector of the IMST im880 board:

|Nucleo CN4 SWD | IMST X1 | Color |
|---|----|---|
| Pin 1: VDD_TARGET (VDD from application) | 15 | Red |
| Pin 2: SWCLK (clock) | 1  | Brown |
| Pin 3: GND (ground) | 16 | Black/Blue |
| Pin 4: SWDIO (SWD data input/output) | 2  | Green |
| Pin 5: NRST (RESET of target STM32) | 5  | Yellow |

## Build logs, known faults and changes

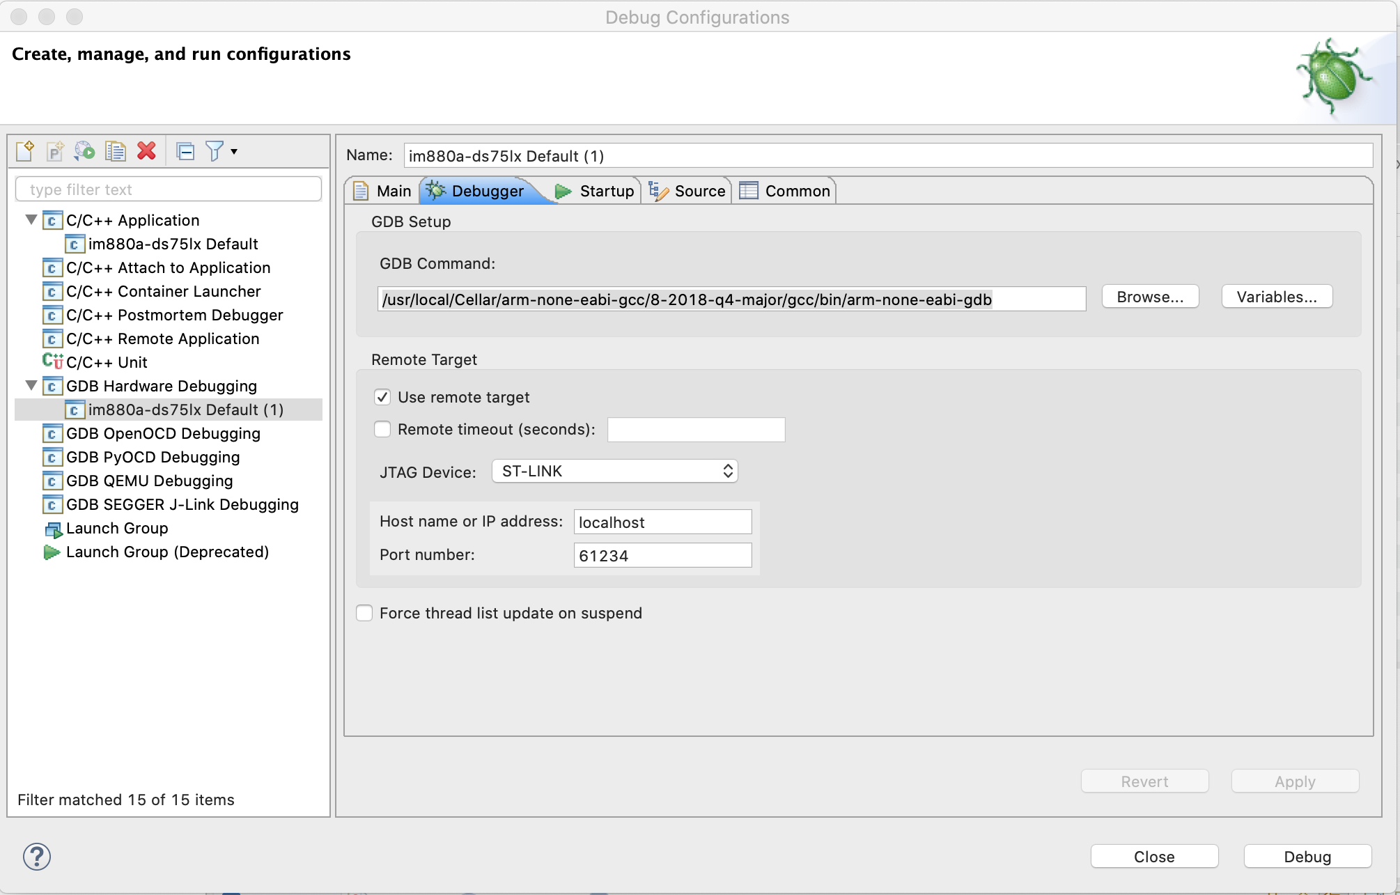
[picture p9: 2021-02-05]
field_test_device/images/debug_config.png

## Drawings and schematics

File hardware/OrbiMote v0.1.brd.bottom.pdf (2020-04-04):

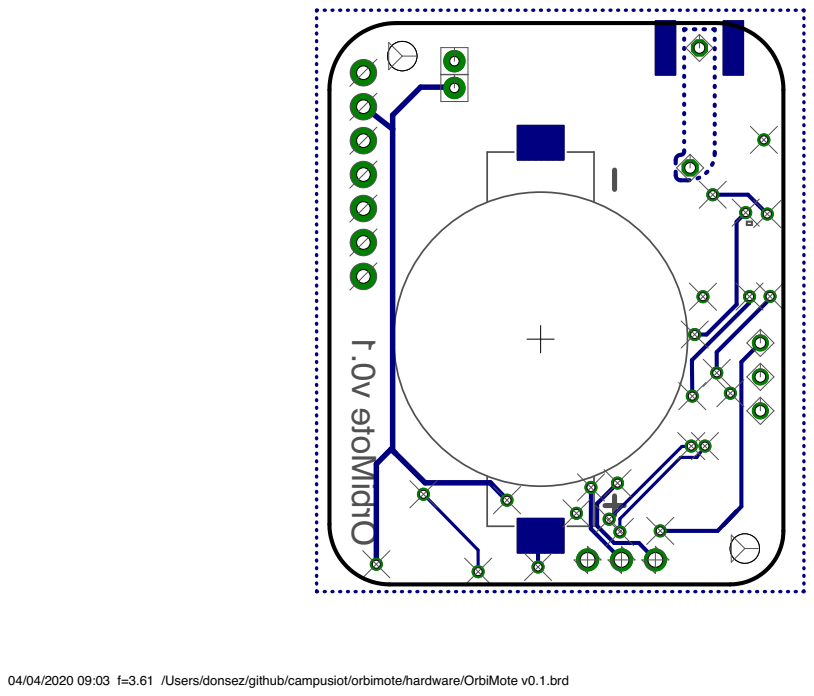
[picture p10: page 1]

04/04/2020 09:03 f=3.61 /Users/donsez/github/campusiot/orbimote/hardware/OrbiMote v0.1.brd

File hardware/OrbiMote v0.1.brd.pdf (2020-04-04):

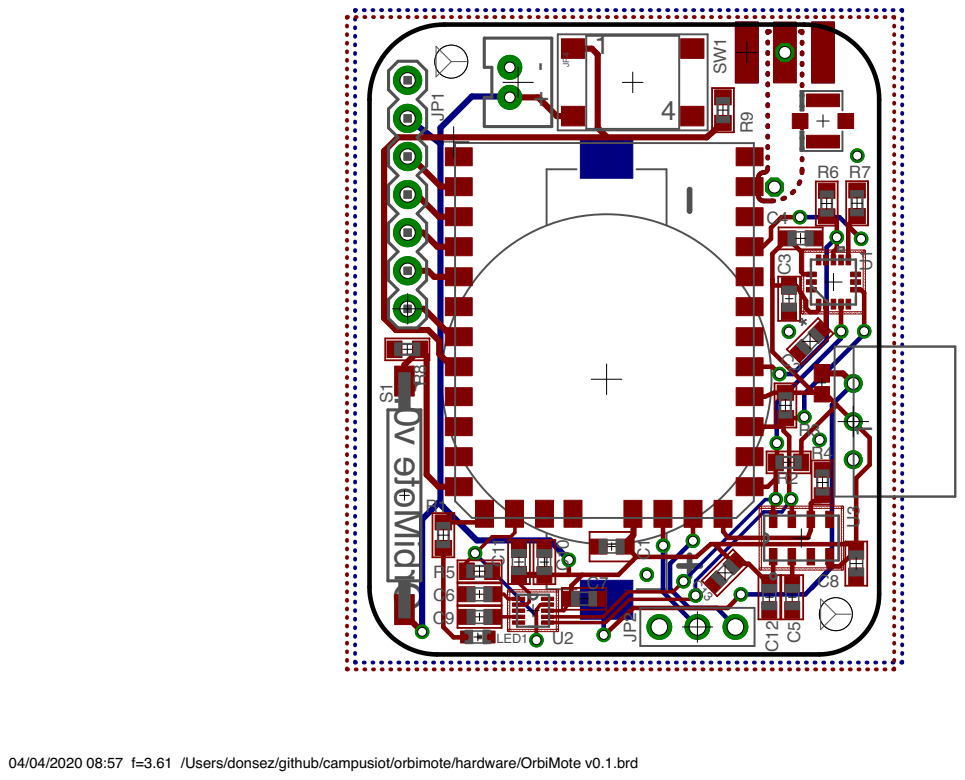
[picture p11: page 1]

04/04/2020 08:57 f=3.61 /Users/donsez/github/campusiot/orbimote/hardware/OrbiMote v0.1.brd

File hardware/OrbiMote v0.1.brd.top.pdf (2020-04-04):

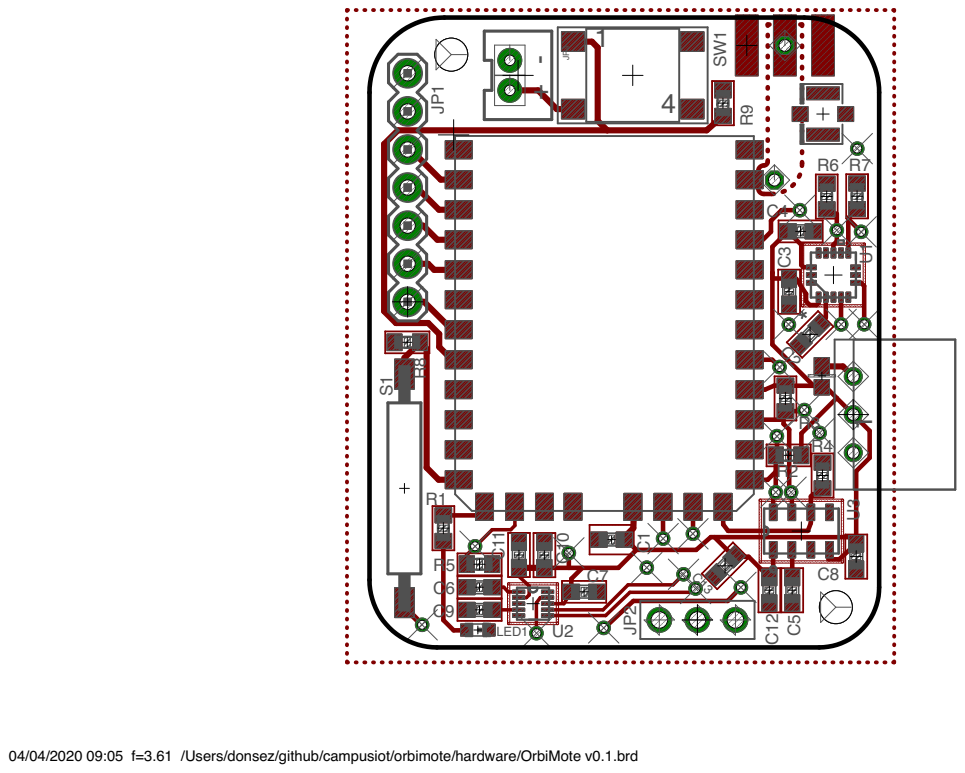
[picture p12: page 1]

04/04/2020 09:05 f=3.61 /Users/donsez/github/campusiot/orbimote/hardware/OrbiMote v0.1.brd

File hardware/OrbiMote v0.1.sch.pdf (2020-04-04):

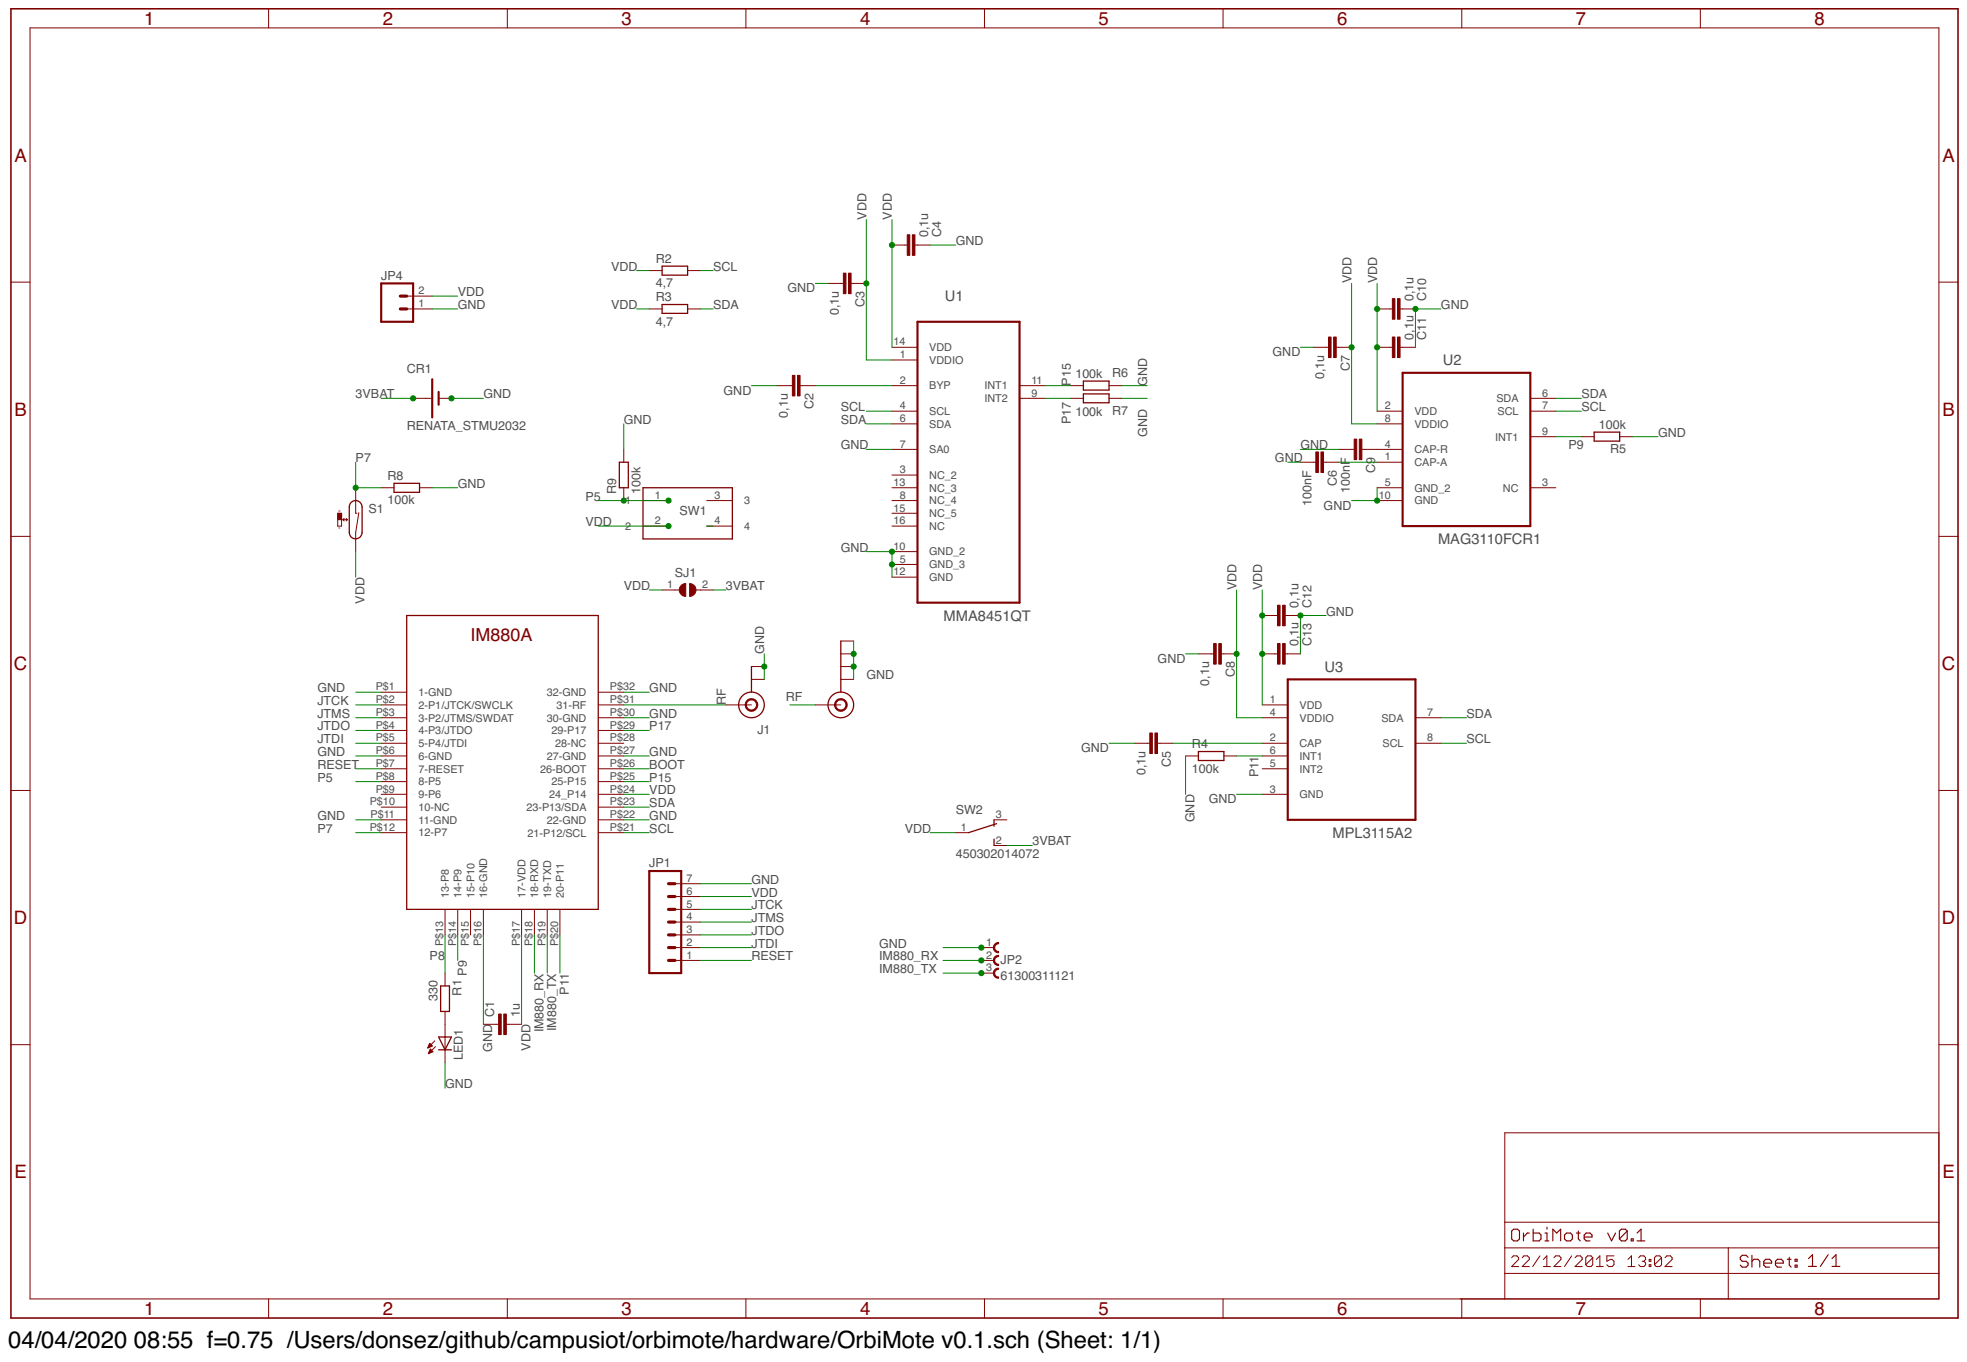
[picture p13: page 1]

04/04/2020 08:55 f=0.75 /Users/donsez/github/campusiot/orbimote/hardware/OrbiMote v0.1.sch (Sheet: 1/1)

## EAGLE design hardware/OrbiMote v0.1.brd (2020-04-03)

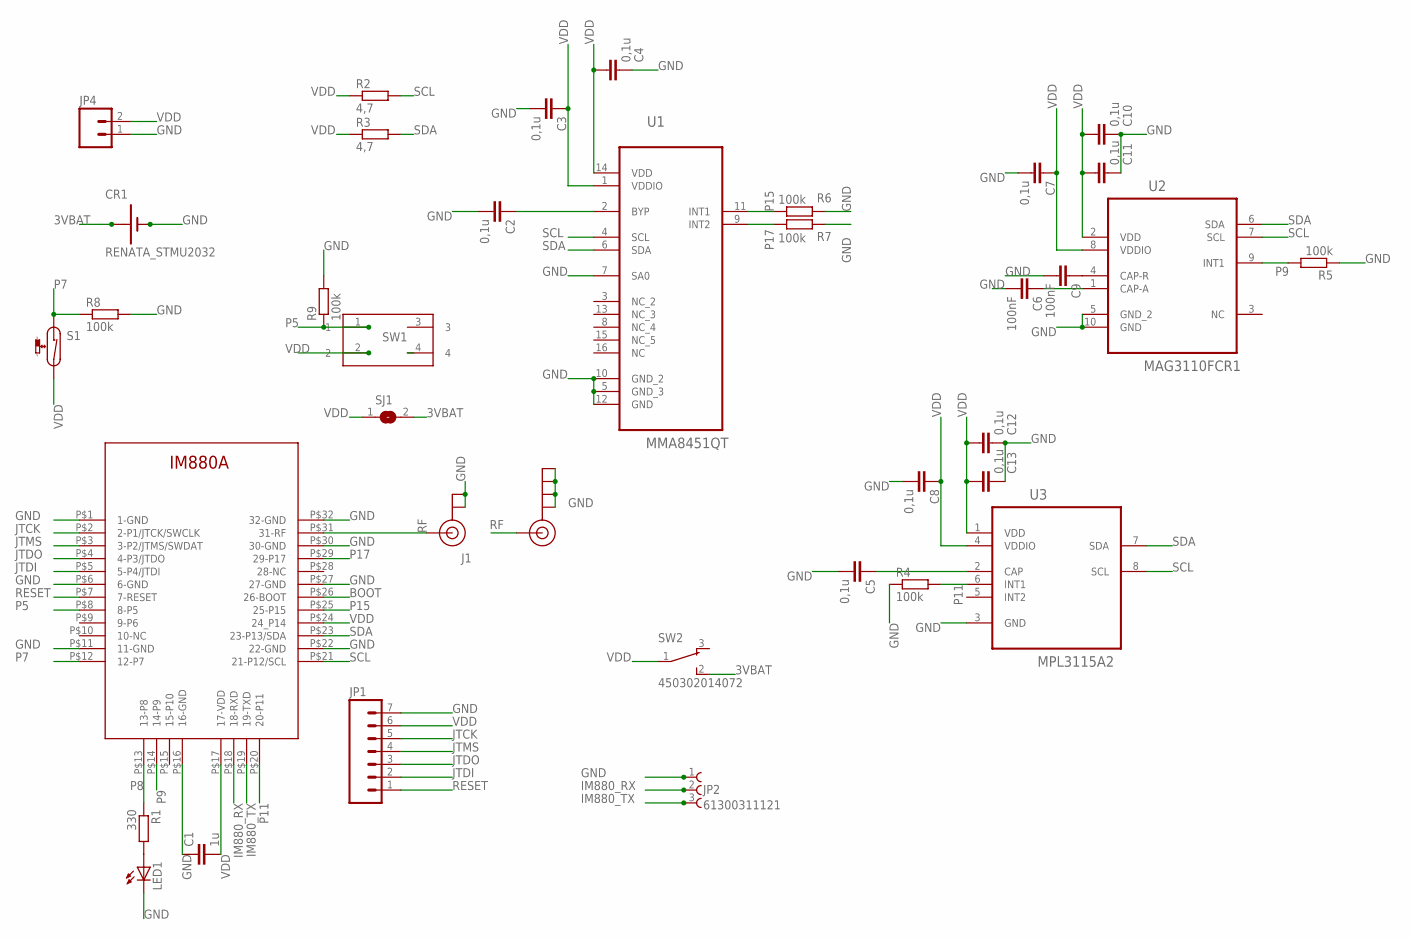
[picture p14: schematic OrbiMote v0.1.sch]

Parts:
C1: 1u; C0603
C2, C3, C4, C5, C7, C8, C10, C11, C12, C13: 0,1u; C0603
C6, C9: 100nF; C0603
CR1: RENATA_STMU2032; SMTU2032
IM1: IM880A
J1: U.FL
J$1: SMA_EDGE; SMA-EDGE
JP1: M07; 1X07
JP2: 61300311121
JP4: M02JST-PTH-VERT; JST-2-PTH-VERT
LED1: LEDCHIPLED_0603; CHIPLED_0603
R1: 330; R0603
R2, R3: 4,7; R0603
R4, R5, R6, R7, R8, R9: 100k; R0603
S1: REED-SWITCH-CT10-1530-G1; CT10-G1
SJ1: SJ
SW1: 430152043826
SW2: 450302014072
U1: MMA8451QT; QFN50P300X300X100-16N
U2: MAG3110FCR1; DFN200X200X90-10N
U3: MPL3115A2; DFN300X500X120-8N

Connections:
3VBAT: CR1.+ (3VBAT), SJ1.2, SW2.2
BOOT: IM1.P$26 (26-BOOT)
GND: C1.1, C2.2, C3.2, C4.2, C5.2, C6.2, C7.2, C8.2, C9.2, C10.2, C11.2, C12.2, C13.2, CR1.-, IM1.P$1 (1-GND), IM1.P$6 (6-GND), IM1.P$11 (11-GND), IM1.P$16 (16-GND), IM1.P$22 (22-GND), IM1.P$27 (27-GND), IM1.P$30 (30-GND), IM1.P$32 (32-GND), J1.P$1 (GND), J1.P$2 (GND), J$1.GND@0 (GND), J$1.GND@1 (GND), J$1.GND@2 (GND), J$1.GND@3 (GND), JP1.7, JP2.1, JP4.1, LED1.C, R4.1, R5.1, R6.1, R7.1, R8.2, R9.2, U1.5 (GND_3), U1.7 (SA0), U1.10 (GND_2), U1.12 (GND), U2.5 (GND_2), U2.10 (GND), U3.3 (GND)
IM880_RX: IM1.P$18 (18-RXD), JP2.2
IM880_TX: IM1.P$19 (19-TXD), JP2.3
JTCK: IM1.P$2 (2-P1/JTCK/SWCLK), JP1.5
JTDI: IM1.P$5 (5-P4/JTDI), JP1.2
JTDO: IM1.P$4 (4-P3/JTDO), JP1.3
JTMS: IM1.P$3 (3-P2/JTMS/SWDAT), JP1.4
unnamed: C2.1, U1.2 (BYP)
unnamed: C5.1, U3.2 (CAP)
unnamed: C9.1, U2.4 (CAP-R)
unnamed: C6.1, U2.1 (CAP-A)
unnamed: LED1.A, R1.2
P5: IM1.P$8 (8-P5), R9.1, SW1.1
P7: IM1.P$12 (12-P7), R8.1, S1.1
P8: IM1.P$13 (13-P8), R1.1
P9: IM1.P$14 (14-P9), R5.2, U2.9 (INT1)
P11: IM1.P$20 (20-P11), R4.2, U3.6 (INT1)
P15: IM1.P$25 (25-P15), R6.2, U1.11 (INT1)
P17: IM1.P$29 (29-P17), R7.2, U1.9 (INT2)
RESET: IM1.P$7 (7-RESET), JP1.1
RF: IM1.P$31 (31-RF), J1.P$3 (SIGNAL), J$1.SIG (SIGNAL)
SCL: IM1.P$21 (21-P12/SCL), R2.2, U1.4 (SCL), U2.7 (SCL), U3.8 (SCL)
SDA: IM1.P$23 (23-P13/SDA), R3.2, U1.6 (SDA), U2.6 (SDA), U3.7 (SDA)
VDD: C1.2, C3.1, C4.1, C7.1, C8.1, C10.1, C11.1, C12.1, C13.1, IM1.P$17 (17-VDD), IM1.P$24 (24_P14), JP1.6, JP4.2, R2.1, R3.1, S1.2, SJ1.1, SW1.2, SW2.1, U1.1 (VDDIO), U1.14 (VDD), U2.2 (VDD), U2.8 (VDDIO), U3.1 (VDD), U3.4 (VDDIO)

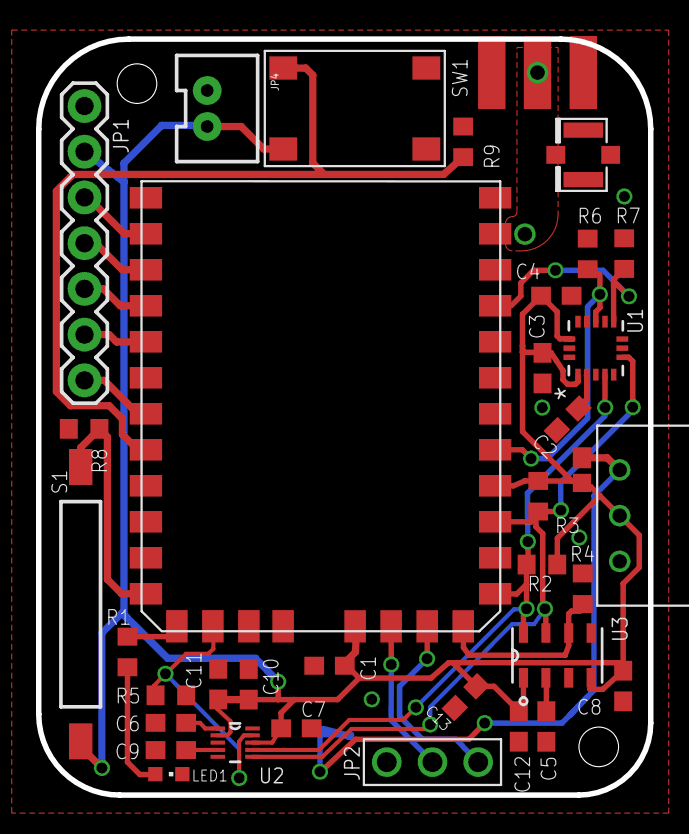
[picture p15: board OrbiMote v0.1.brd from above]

Board: 2 copper layers, 34.0 x 42.0 mm, 37 parts (1 on the bottom side), 25 nets.

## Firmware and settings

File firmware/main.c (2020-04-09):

/*
 * Read pediodically the measurements from the board sensors
 * then send to the LoRaWAN network in which the endpoint is registered.
 * The payload format is LPP Cayenne.
 * 
 * Copyright (C) 2020 LIG Université Grenoble Alpes
 *
 * This file is subject to the terms and conditions of the GNU Lesser
 * General Public License v2.1. See the file LICENSE in the top level
 * directory for more details.
 */

#define ENABLE_DEBUG (1)
#include "debug.h"

#include <string.h>

#include "xtimer.h"
#include <time.h>

#include "mutex.h"
#include "periph_conf.h"
#include "periph/rtc.h"

#include "board.h"

#include "fmt.h"

#include "net/loramac.h"
#include "semtech_loramac.h"
#include "loramac_utils.h"
#include "cayenne_lpp.h"

// NXP MPL3115A2: 20 to 110 kPa, Absolute Digital Pressure Sensor
#include "mpl3115a2.h"
#include "mpl3115a2_params.h"

// NXP MMA8451Q, 3-axis, 14-bit/8-bit digital accelerometer
// #include "mma8x5x.h"
// #include "mma8x5x_params.h"

// NXP Xtrinsic MAG3110 Three-Axis, Digital Magnetometer
// #include "mag3110.h"
// #include "mag3110_params.h"

#include "time_utils.h"

/* Declare globally the loramac descriptor */
static semtech_loramac_t loramac;

/* Declare globally the sensor device descriptor */
static mpl3115a2_t dev;

/* Cayenne LPP buffer */
static cayenne_lpp_t lpp;

/* LoRaMac values */
#define JOIN_NEXT_RETRY_TIME            120 // Next join tentative in 2 minute(s)
#define SECONDS_PER_DAY                 24 * 60 * 60

/* Use a fast datarate, e.g. BW125/SF7 in EU868 */
#define DR_INIT                         LORAMAC_DR_5
#define ADR_ON                          true

#define FIRST_TX_PERIOD                 120 // First Tx period 2 minutes
#define TX_PERIOD                       120 // Tx period 2 minutes

#define PORT_UP_DATA                    1
#define PORT_UP_GET_EPOCH               2
#define PORT_UP_ERROR                   99

#define PORT_DN_TEXT                    1
#define PORT_DN_EPOCH                   2
#define PORT_DN_SET_TX_PERIOD           3

#define SLEEP_USEC  (1UL * US_PER_SEC)


/* Implement the receiver thread */
#define RECEIVER_MSG_QUEUE                          (4U)

#ifdef FORGE_DEVEUI_APPEUI_APPKEY
static uint8_t secret[LORAMAC_APPKEY_LEN];
#endif

static uint8_t deveui[LORAMAC_DEVEUI_LEN];
static uint8_t appeui[LORAMAC_APPEUI_LEN];
static uint8_t appkey[LORAMAC_APPKEY_LEN];

static msg_t _receiver_queue[RECEIVER_MSG_QUEUE];
static char _receiver_stack[THREAD_STACKSIZE_DEFAULT];

static uint32_t epoch = 0;
static bool epoch_set = false;
static struct tm current_time;

static uint16_t tx_period = TX_PERIOD;

static void init_sensors(void){
    uint8_t port = PORT_UP_DATA;
    if (mpl3115a2_init(&dev, &mpl3115a2_params[0]) != MPL3115A2_OK) {
    	DEBUG("[FAILED] init mpl3115a2!");
        port = PORT_UP_ERROR;
    }
    semtech_loramac_set_tx_port(&loramac, port);
}

static void print_sensors(void)
{
    // TODO si l'initialisation du mpl3115a2 a échoué, il faut envoyer un message avec le fPort PORT_UP_ERROR

    if (mpl3115a2_set_active(&dev) != MPL3115A2_OK) {
    	DEBUG("[FAILED] activate mpl3115a2!");
        return;
    }
    uint32_t pressure;
    int16_t temperature;
    uint8_t status;
    xtimer_usleep(SLEEP_USEC);
    if ((mpl3115a2_read_pressure(&dev, &pressure, &status) |
            mpl3115a2_read_temp(&dev, &temperature)) != MPL3115A2_OK) {
    	DEBUG("[FAILED] read values from mpl3115a2!");
        return;
    }
    else {
    	DEBUG("mpl3115a2: pressure=%u Pa, temperature=%3d.%d C, state=%#02x\n",
                (unsigned int)pressure, temperature/10, abs(temperature%10), status);
    }

    if (mpl3115a2_set_standby(&dev) != MPL3115A2_OK) {
    	DEBUG("[FAILED] standby mpl3115a2!");
        return;
    }
}


static void read_sensors(cayenne_lpp_t* lpp){
    // TODO si l'initialisation du ds75lx a échoué, il faut envoyer un message avec le fPort PORT_UP_ERROR

    if (mpl3115a2_set_active(&dev) != MPL3115A2_OK) {
    	DEBUG("[FAILED] activate mpl3115a2!");
        return;
    }
    uint32_t pressure;
    int16_t temperature;
    uint8_t status;
    xtimer_usleep(SLEEP_USEC);
    if ((mpl3115a2_read_pressure(&dev, &pressure, &status) |
            mpl3115a2_read_temp(&dev, &temperature)) != MPL3115A2_OK) {
    	DEBUG("[FAILED] read values from mpl3115a2!");
        return;
    }
    else {
    	DEBUG("mpl3115a2: pressure=%u Pa, temperature=%3d.%d C, state=%#02x\n",
                (unsigned int)pressure, temperature/10, abs(temperature%10), status);
        cayenne_lpp_add_temperature(lpp, 0, (float)temperature / 10);
        cayenne_lpp_add_barometric_pressure(lpp, 1, (float)pressure);
    }

    if (mpl3115a2_set_standby(&dev) != MPL3115A2_OK) {
    	DEBUG("[FAILED] standby mpl3115a2!");
        return;
    }
}

static void sender(void)
{
    while (1)
    {
        /* read the sensors values and add them to lpp */
        read_sensors(&lpp);

        /* send the LoRaWAN message */
        uint8_t ret = semtech_loramac_send(&loramac, lpp.buffer, lpp.cursor);

        if (ret != SEMTECH_LORAMAC_TX_DONE)
        {
            DEBUG("Cannot send LPP payload: ret code: %d (%s)\n", ret, semtech_loramac_err_message(ret));
        }

        /* clear buffer once done */
        cayenne_lpp_reset(&lpp);

        /* sleep tx_period secs */
        // TODO introduire un alea de quelques secondes dans la tx_period pour éviter que des endpoints qui redémarrent ensemble se brouillent les uns les autres.
        // TODO verifier que la tx_period est compatible avec le DC (sinon, le Tx retourne le code=13)
        xtimer_sleep(tx_period);
    }

    /* this should never be reached */
    return;
}

static void *receiver(void *arg)
{
    msg_init_queue(_receiver_queue, RECEIVER_MSG_QUEUE);

    (void)arg;
    while (1) {
        rtc_get_time(&current_time);
        print_time("Clock value is now ", &current_time);

        /* blocks until something is received */
        switch (semtech_loramac_recv(&loramac)) {
            case SEMTECH_LORAMAC_RX_DATA:
                // TODO process Downlink payload
                switch(loramac.rx_data.port) {
                    case PORT_DN_TEXT:
                        loramac.rx_data.payload[loramac.rx_data.payload_len] = 0;
                        DEBUG("Data received: text=%s, port: %d \n",
                            (char *)loramac.rx_data.payload, loramac.rx_data.port);
                        break;
                    case PORT_DN_EPOCH:
                        if(loramac.rx_data.payload_len == sizeof(epoch)) {
                            epoch=*((uint32_t*)loramac.rx_data.payload);
                            DEBUG("Data received: epoch=%ld, port: %d\n",
                                epoch, loramac.rx_data.port);
                            struct tm new_time;
                            epoch_to_time(&new_time, epoch);
                            rtc_set_time(&new_time);
                            print_time("Clock value is set to ", &new_time);
                            epoch_set = true;

                        } else {
                            DEBUG("Data received: bad size for epoch, port: %d\n",
                                 loramac.rx_data.port);
                        }
                        break;
                    case PORT_DN_SET_TX_PERIOD:
                        if(loramac.rx_data.payload_len == sizeof(tx_period)) {
                            tx_period=*((uint16_t*)loramac.rx_data.payload);
                            DEBUG("Data received: tx_period=%d, port: %d\n",
                                tx_period, loramac.rx_data.port);
                        } else {
                            DEBUG("Data received: bad size for tx_period, port: %d\n",
                                 loramac.rx_data.port);
                        }
                        break;
                    default:
                        DEBUG("Data received: ");
                        printf_ba(loramac.rx_data.payload, loramac.rx_data.payload_len);
                        DEBUG(", port: %d\n",loramac.rx_data.port);
                        break;
                }
                break;

            case SEMTECH_LORAMAC_RX_CONFIRMED:
                // TODO if too much unconfirmed Tx frames --> rejoin
                DEBUG("Received ACK from network\n");
                break;

            default:
                break;
        }
    }
    return NULL;
}

/**
 * main function
 * TODO add LED, button, add reed switch
 * TOOD add GPS parsing on UART RX pin (UART TX pin is used by the console)
 */
int main(void)
{
    /* read RTC */
    rtc_get_time(&current_time);
    print_time("Clock value is now ", &current_time);

    /* initialize the sensors */
    init_sensors();

    /* print the current values of the sensors */
    print_sensors();

    /* initialize the loramac stack */
    semtech_loramac_init(&loramac);

    /* set ADR flag */
    semtech_loramac_set_adr(&loramac, ADR_ON);

#ifdef FORGE_DEVEUI_APPEUI_APPKEY
    /* forge the deveui, appeui and appkey of the endpoint */
    fmt_hex_bytes(secret, SECRET);
    loramac_forge_deveui(deveui,appeui,appkey,secret);
    DEBUG("Secret:"); printf_ba(secret,LORAMAC_APPKEY_LEN); DEBUG("\n");
#else
    /* Convert identifiers and application key */
    fmt_hex_bytes(deveui, DEVEUI);
    fmt_hex_bytes(appeui, APPEUI);
    fmt_hex_bytes(appkey, APPKEY);
#endif
    DEBUG("DevEUI:"); printf_ba(deveui,LORAMAC_DEVEUI_LEN); DEBUG("\n");
    DEBUG("AppEUI:"); printf_ba(appeui,LORAMAC_APPEUI_LEN); DEBUG("\n");
    DEBUG("AppKey:"); printf_ba(appkey,LORAMAC_APPKEY_LEN); DEBUG("\n");

    /* set the LoRaWAN keys */
    semtech_loramac_set_deveui(&loramac, deveui);
    semtech_loramac_set_appeui(&loramac, appeui);
    semtech_loramac_set_appkey(&loramac, appkey);

    /* start the OTAA join procedure (and retries in required) */
    /*uint8_t joinRes = */ loramac_join_retry_loop(&loramac, DR_INIT, JOIN_NEXT_RETRY_TIME, SECONDS_PER_DAY);

    /* start the receiver thread */
    thread_create(_receiver_stack, sizeof(_receiver_stack),
                  THREAD_PRIORITY_MAIN - 1, 0, receiver, NULL, "receiver thread");

    /* sleep FIRST_TX_PERIOD secs */
    xtimer_sleep(FIRST_TX_PERIOD);

    /* call the sender */
    sender();
    
    return 0; /* should never be reached */
}

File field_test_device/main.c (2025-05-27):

/*
 * Read pediodically the temperature from the DS75LX sensor
 * then send to the LoRaWAN network in which the endpoint is registered.
 * The payload format is LPP Cayenne.
 * 
 * Copyright (C) 2020-2022 LIG Université Grenoble Alpes
 *
 * This file is subject to the terms and conditions of the GNU Lesser
 * General Public License v2.1. See the file LICENSE in the top level
 * directory for more details.
 *
 * @author Didier DONSEZ
 */

#define ENABLE_DEBUG (1)
#include "debug.h"

#include <string.h>

#include "xtimer.h"
#include <time.h>

#include "mutex.h"
#include "periph_conf.h"
#include "periph/rtc.h"
#include "periph/pm.h"

#include "cpu_conf.h"
#include "periph/cpuid.h"

#include "board.h"

#include "fmt.h"

//#include "net/loramac.h"
#include "semtech_loramac.h"
#include "loramac_utils.h"

#include "git_utils.h"
#include "wdt_utils.h"

#if DS75LX == 1
#include "ds75lx.h"
#include "ds75lx_params.h"
#endif

#if AT30TES75X == 1
#include "at30tse75x.h"
#endif

#if MODULE_MAG3110 == 1
#include "mag3110.h"
#include "mag3110_params.h"
#endif

#if MODULE_MMA8X5X == 1
#include "mma8x5x.h"
#include "mma8x5x_params.h"
#endif

#if MODULE_MPL3115A2 == 1
#include "mpl3115a2.h"
#include "mpl3115a2_params.h"
#endif


#if MODULE_BME680 == 1
#include "bme680.h"
#include "bme680_params.h"
#endif

#if GPS == 1
#include "gps.h"
#endif

#include "app_clock.h"
#include "benchmark.h"

#include <random.h>

/* Declare globally the loramac descriptor */
extern semtech_loramac_t loramac;

/* Declare globally the sensor device descriptor */
#if MODULE_DS75LX == 1
ds75lx_t ds75lx;
#endif

#if MODULE_AT30TES75X == 1
at30tse75x_t at30tse75x;
#endif

#if MODULE_MAG3110 == 1
static mag3110_t mag3110;
#endif

#if MODULE_MMA8X5X == 1
static mma8x5x_t mma8x5x;
#endif

#if MODULE_MPL3115A2 == 1
static mpl3115a2_t mpl3115a2;
#endif

// Count the number of elements in an array.
#define CNT(array) (uint8_t)(sizeof(array) / sizeof(*array))

/* LoRaMac values */
#define JOIN_NEXT_RETRY_TIME            10 // Next join tentative in 1 minute
#define SECONDS_PER_DAY                 24 * 60 * 60

/* Use a fast datarate, e.g. BW125/SF7 in EU868 */
#define DR_INIT                         LORAMAC_DR_5

#define FIRST_TX_PERIOD                 TXPERIOD
#define TX_PERIOD                       TXPERIOD

#define PORT_UP_DATA                    101
#define PORT_UP_ERROR                   102

#define PORT_DN_TEXT                    101
#define PORT_DN_SET_TX_PERIOD           3
#define PORT_DN_REBOOT_NOW           	64
#define PORT_DN_REBOOT_ONE_MINUTE       65
#define PORT_DN_REBOOT_ONE_HOUR         66


#ifndef VIRT_DEV
#define VIRT_DEV 						(1U)
#endif


/* Implement the receiver thread */
#define RECEIVER_MSG_QUEUE                          (4U)

#if OTAA == 1

#ifdef FORGE_DEVEUI_APPEUI_APPKEY
static uint8_t secret[LORAMAC_APPKEY_LEN];
#endif

static uint8_t deveui[LORAMAC_DEVEUI_LEN] ;
static uint8_t appeui[LORAMAC_APPEUI_LEN] ;
static uint8_t appkey[LORAMAC_APPKEY_LEN] ;

#else

// static uint32_t* devaddr = { DEVADDRS };

static uint8_t devaddr[LORAMAC_DEVADDR_LEN] ;
static uint8_t appskey[LORAMAC_NWKSKEY_LEN] ;
static uint8_t nwkskey[LORAMAC_APPSKEY_LEN] ;

#endif

static msg_t _receiver_queue[RECEIVER_MSG_QUEUE];
static char _receiver_stack[THREAD_STACKSIZE_DEFAULT];

static uint16_t tx_period = TX_PERIOD;

static void init_sensors(void){

    uint8_t port = PORT_UP_DATA;
    int result;

	(void) result;

#if GPS == 1
    DEBUG("[gps] GPS is enabled (baudrate=%d)\n",STD_BAUDRATE);
#endif

#if MODULE_DS75LX == 1
    DEBUG("[ds75lx] DS75LX sensor is enabled\n");

    result = ds75lx_init(&ds75lx, &ds75lx_params[0]);
    if (result != DS75LX_OK)
    {
        DEBUG("[error] Failed to initialize DS75LX sensor\n");
        port = PORT_UP_ERROR;
    }
#endif

#if MODULE_AT30TES75X == 1
    DEBUG("[at30tse75x] AT30TES75X sensor is enabled\n");

    result = at30tse75x_init(&at30tse75x, PORT_A, AT30TSE75X_TEMP_ADDR);
    if (result != 0)
    {
        DEBUG("[error] Failed to initialize AT30TES75X sensor\n");
        port = PORT_UP_ERROR;
    }
#endif

#if MODULE_MAG3110 == 1
    puts("MAG3110 magnetometer driver test application\n");
    printf("Initializing MAG3110 magnetometer at I2C_%i... ",
           mag3110_params[0].i2c);
    if (mag3110_init(&mag3110, &mag3110_params[0]) != MAG3110_OK) {
        DEBUG("[error] Failed to initialize MAG3110 sensor\n");
        port = PORT_UP_ERROR;
    }
#endif

#if MODULE_MMA8X5X == 1
    puts("MMA8652 accelerometer driver test application\n");
    printf("Initializing MMA8652 accelerometer at I2C_DEV(%i)... ", mma8x5x_params->i2c);

    result = mma8x5x_init(&mma8x5x, mma8x5x_params);
    if(result != MMA8X5X_OK) {
    	DEBUG("[error] Failed to initialize MMA8X5X sensor\n");
    	port = PORT_UP_ERROR;
    }
#endif

#if MODULE_MPL3115A2 == 1
	result = mpl3115a2_init(&mpl3115a2, &mpl3115a2_params[0]);
	if(result != MPL3115A2_OK) {
    	DEBUG("[error] Failed to initialize MMA8X5X sensor\n");
    	port = PORT_UP_ERROR;
	}

	if (mpl3115a2_set_active(&mpl3115a2) != MPL3115A2_OK) {
		puts("[FAILED] activate measurement!");
		port = PORT_UP_ERROR;
	}
#endif


    semtech_loramac_set_tx_port(&loramac, port);
}

// Encode message data to the payload.
unsigned int encode_sensors(uint8_t *payload, const unsigned int len) {

	if(len < sizeof(int16_t)) {
		return 0;
	}

	int16_t temperature = 0;

#if MODULE_DS75LX == 1
	{
    /* measure temperature */
    ds75lx_wakeup(&ds75lx);
    /* Get temperature in degrees celsius */
    ds75lx_read_temperature(&ds75lx, &temperature);
    ds75lx_shutdown(&ds75lx);
    DEBUG("[ds75lx] get temperature : temperature=%d\n",temperature);
	}
#endif

#if MODULE_AT30TES75X == 1
    {
    /* measure temperature */
    //at30tse75x_wakeup(&at30tse75x);
    /* Get temperature in degrees celsius */
    float ftemp;
    at30tse75x_get_temperature(&at30tse75x, &ftemp);
    temperature = (int16_t)(ftemp * 100);
    //at30tse75x_shutdown(&at30tse75x);
    DEBUG("[at30tse75x] get temperature : temperature=%d\n",temperature);
    }
#endif

    unsigned int i = 0;

    // Encode temperature.
	payload[i++] = (temperature >> 8) & 0xFF;
	payload[i++] = (temperature >> 0) & 0xFF;

	if(len < i + (3*4)) {
		return i;
	}

#if MODULE_MAG3110 == 1
    {
    mag3110_data_t data;
    int8_t temp;
    mag3110_read(&mag3110, &data);
    printf("Field strength: X: %d Y: %d Z: %d\n", data.x, data.y, data.z);
    mag3110_read_dtemp(&mag3110, &temp);
    printf("Die Temperature T: %d\n", temp);
    // TODO add to payload
    }
#endif

	if(len < i + (3*4)) {
		return i;
	}

#if MODULE_MMA8X5X == 1
    {
    mma8x5x_data_t data;
    mma8x5x_read(&mma8x5x, &data);

    printf("Acceleration [in mg]: X: %d Y: %d Z: %d\n", data.x, data.y, data.z);
    // TODO add to payload
    }
#endif

    if(len < i + (2+2+1)) {
		return i;
	}
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

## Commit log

2020-04-10 add Amphenol Pressure Sensors
2021-02-05 add field test device firmware
2021-02-27 add boards list
2021-02-27 add boards
2021-07-17 improve Makefile for device customization
2021-07-26 print nwkskey and appskey after otaa join procedure
2022-03-04 fix devaddr print
2022-06-07 add downlinks for rebooting
    [main.c]
2022-06-08 add idosens boards
2025-05-27 add todo for i2c scanner
2026-06-10 add debug trace for APP_CLOCK_SYNC

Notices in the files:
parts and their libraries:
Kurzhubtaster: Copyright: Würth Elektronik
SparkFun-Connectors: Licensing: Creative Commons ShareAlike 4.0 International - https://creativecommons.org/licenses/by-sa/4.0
